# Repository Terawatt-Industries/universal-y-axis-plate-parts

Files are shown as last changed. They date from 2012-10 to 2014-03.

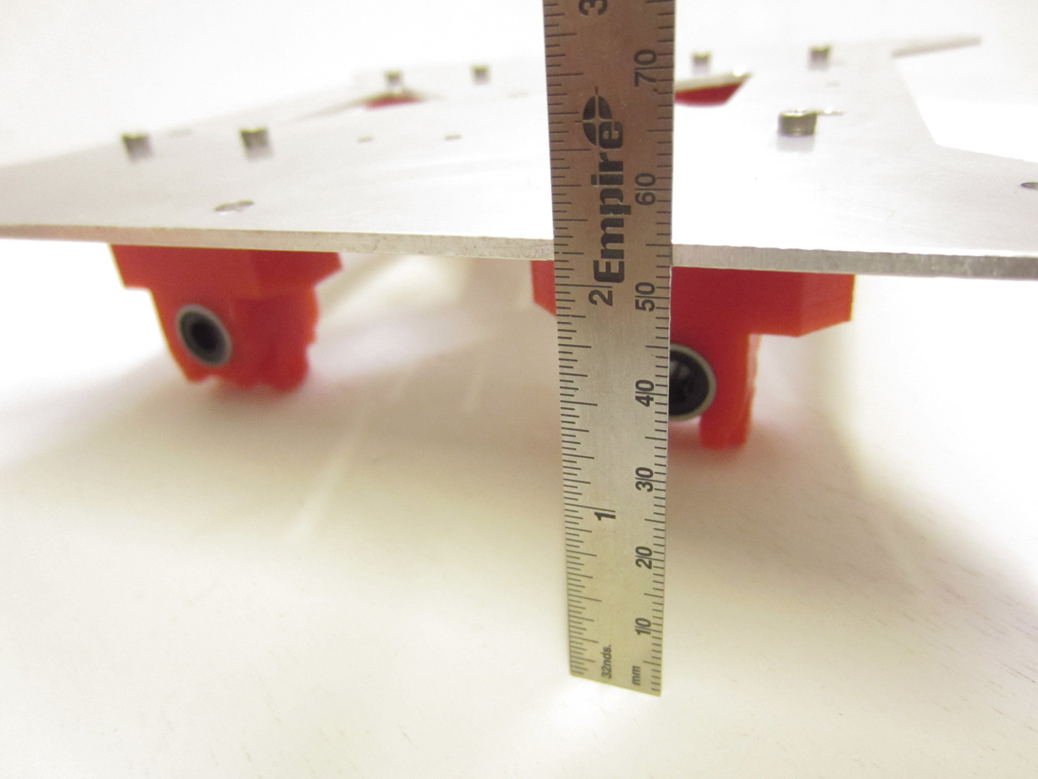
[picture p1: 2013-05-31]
img/plate_with_mounts.JPG

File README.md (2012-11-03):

##Universal Y-Axis Plate
The Universal Y-Axis Plate is an aluminum y-axis plate for RepRap printers, with matching open-source 3D-printed parts to mount it.

The universal plate is designed to eliminate the y-axis plate, and combines both y-axis and heatbed plate holes in one design.  The plate is designed and fulfilled by Terawatt Industries.

This repository contains the matching printed (plastic) parts for the universal plate.  All design files are SCAD with some basic paramterization for height.  There are mounts for LM8UU bearings and tensioners with extra height to keep the belt aligned.

##Bill of Materials
Terawatt fulfills this BOM with 18-8 stainless hardware, but any steel alloy is OK.

1. 1x Universal Y-Axis Plate
2. 8x M3 x 40-45mm socket cap screws
3. 4x M3 x 20-25mm socket cap screws
4. 12x M3 nuts
5. 8x M3 Fender Washer
6. 4x printed LM8UU mount spacers (PLA recommended w/high infill ratio)
7. 4x printed LM8UU mounts (PLA recommended w/high infill ratio)
8. 4x LM8UU bearings

##Assembly Instructions
1. Print up the parts required in PLA, or obtain them.
2. Attach a spacer to the plate with 2x M3x45mm screws.  It may be a tight fit that requires a hex wrench to thread completely.  Then attach the LM8UU mounts on top.
3. Place nuts in the traps and tighten each screw evenly.
4. Repeat steps 2-3 for the other 3 mounts.
5. Push LM8UU bearings into the mounts from the sides.  A bearing press makes the job easier.
6. Place an M3x20mm screw in the mount and a nut in the opposite trap.
7. Tighten the screw.  Be careful not to overtension!  The mount will break if overtensioned - when you hear the plastic stress it's time to stop!
8. Repeat steps 6-7 for each mount.

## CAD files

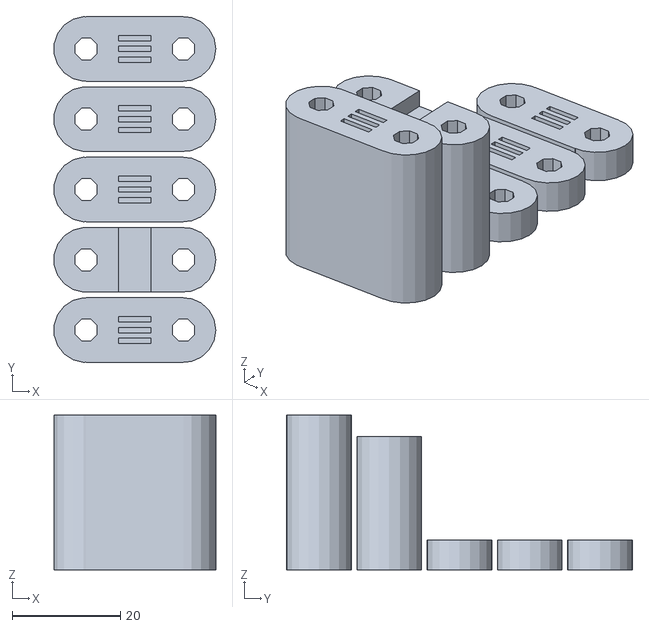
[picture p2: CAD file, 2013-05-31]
dist/belt_tensioner.stl
29.9 x 64.0 x 28.6

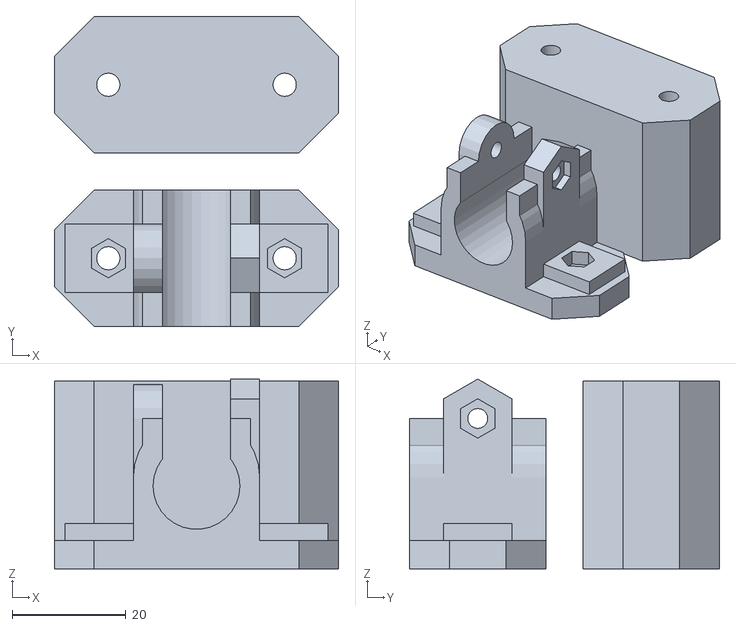
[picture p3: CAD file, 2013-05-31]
dist/lm8uu_with_spacer.stl
50.0 x 54.5 x 33.4

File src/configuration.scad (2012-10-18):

// PRUSA Mendel  
// Configuration file
// GNU GPL v2
// Josef Průša
// josefprusa@me.com
// prusadjs.cz
// http://www.reprap.org/wiki/Prusa_Mendel
// http://github.com/prusajr/PrusaMendel

// PLEASE SELECT ONE OF THE CONFIGURATIONS BELOW
// BY UN-COMMENTING IT

variant=0; //0 for metric
//variant=1; //1 for SAE
if(variant==0){
echo("variant: metric");
}else if(variant==1){
echo("variant: sae");
} else{
echo("WARNING: INVALID CONFIGURATION");
}


vars=[
//[m8_dia, m8_nut, m4_dia, m4_nut, m3_dia, m3_nut, bush_dia, mot_shaft, bush_rod, bush_outerdia, bush_length]
[9,16.4,5,9,4.4,7,11,5.3,8,16,11],//metric
[9,15.7,5.5,10.6,5.5,10.6,11.5,5.3,7.9375,16,11]//SAE
];

//BUSHING TYPE Can generate three versions
// 1 - regular old ones
// 2 - helical ones
// 3 - holders for brass or any other bought bushings
bushing_type = 2;

//Round corner diameter
round_corner_diameter = 8;

//Thin wall size
layer_height = 0.3;
perimeter_width_over_thicknes = 1.6;
infill_widht_over_thickness = 1.55;
thin_wall = 2*(perimeter_width_over_thicknes*layer_height+infill_widht_over_thickness*layer_height);
if(thin_wall<2){
	echo("Check thin wall size, its below 2mm!");
}
echo(thin_wall);

//DO NOT TOUCH THIS SECTION!
m8_diameter = vars[variant][0];
m8_nut_diameter = vars[variant][1];
m4_diameter = vars[variant][2];
m4_nut_diameter = vars[variant][3];
m3_diameter = vars[variant][4];
m3_nut_diameter = vars[variant][5];
bushing_diameter = vars[variant][6];
motor_shaft=vars[variant][7];
bushing_rodsize = vars[variant][8];
bushing_outerDiameter = vars[variant][9];
bushing_lenght = vars[variant][10];


// MINI-HUXLEY VERSION (TODO, just place holder)
// include <configuration-huxley.scad>

// MEGA VERSION (TODO, just place holder)
// include <configuration-mega.scad>


// Some basic functions, probably should be somewhere else
module roundcorner(diameter){
	difference(){
		cube(size = [diameter,diameter,99], center = false);
		translate(v = [diameter, diameter, 0]) cylinder(h = 100, r=diameter, center=true);
	}
}

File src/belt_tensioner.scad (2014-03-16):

// Gregs configuration file
include <configuration.scad>

$fn = 20;

belt_width=6;
belt_thickness=1.5; 
tooth_height=1.5;
tooth_spacing=2;

belt_clamp_thickness=15.5; 
//belt_clamp_width=m3_diameter+3*belt_clamp_thickness+2;
belt_clamp_width = 12;

belt_clamp_hole_separation=18;

belt_clamp_height=m3_diameter+2*belt_clamp_thickness;
belt_clamp_length=belt_clamp_hole_separation+m3_diameter+2*belt_clamp_thickness;

belt_clamp_channel_height=belt_thickness+tooth_height+belt_clamp_thickness*1.4;
belt_clamp_clamp_height=tooth_height+belt_clamp_thickness*1.75;

for (i=[-1])
translate([0,i*(belt_clamp_width+1),0])
belt_clamp(belt_clamp_clamp_height);

belt_clamp_channel(belt_clamp_channel_height);

for (i=[1,2,3])
translate([0,i*(belt_clamp_width+1),0])
belt_clamp(5.5);

module belt_clamp_socket(bch)
{
	difference()
	{
		translate([0,0,bch/2])
		union()
		{
			cube([belt_clamp_hole_separation,belt_clamp_width,bch],center=true);
			for(i=[-1,1])
			translate([i*belt_clamp_hole_separation/2,0,0])
			cylinder(r=belt_clamp_width/2,h=bch,center=true);
		}
		belt_clamp_holes(bch + 2);
	}
}

module belt_clamp_channel(bcchh = belt_clamp_channel_height)
{
	difference()
	{
		translate([0,0,bcchh/2])
		union()
		{
			cube([belt_clamp_hole_separation,belt_clamp_width,bcchh],center=true);
			for(i=[-1,1])
			translate([i*belt_clamp_hole_separation/2,0,0])
			cylinder(r=belt_clamp_width/2,h=bcchh,center=true);
		}

		belt_clamp_holes(belt_clamp_height + 2);

		translate([-belt_width/2,-belt_clamp_width/2-1,bcchh - belt_thickness-tooth_height])
		cube([belt_width,belt_clamp_width+2,belt_thickness+tooth_height+1]);
	}
}

module belt_clamp_holes(height = belt_clamp_height)
{
	translate([0,0,belt_clamp_height/2])
	{
		for(i=[-1,1])
		translate([i*belt_clamp_hole_separation/2,0,0])
		cylinder(r=m3_diameter/2,h=height,center=true);	
	}
}

module belt_clamp(bcch = belt_clamp_clamp_height)
{
	difference()
	{
		translate([0,0,bcch/2])
		union()
		{
			cube([belt_clamp_hole_separation,belt_clamp_width,bcch],center=true);
			for(i=[-1,1])
			translate([i*belt_clamp_hole_separation/2,0,0])
			cylinder(r=belt_clamp_width/2,h=bcch,center=true);
		}
		belt_clamp_holes();
		for(i=[-1:1])
		translate([-belt_width/2,-tooth_spacing/4+i*tooth_spacing,bcch - tooth_height])
		cube([belt_width,tooth_spacing/2,tooth_height+1]);
	}
}

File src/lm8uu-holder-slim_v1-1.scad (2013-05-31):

// LM8UU holder slim v1.1
// *********************************************
// Jonas Kühling
// http://www.jonaskuehling.de
// http://www.thingiverse.com/jonaskuehling
// *********************************************
// derived from:
// http://www.thingiverse.com/thing:14942

// LM8UU/rod dimensions
LM8UU_dia = 15.2;
LM8UU_length = 24;
rod_dia = 8;

//screw/nut dimensions (M3) - hexagon socket head cap screw ISO 4762, hexagon nut ISO 4032
screw_thread_dia_iso = 3;
screw_head_dia_iso = 5.5;
nut_wrench_size_iso = 5.5;


// screw/nut dimensions for use (plus clearance for fitting purpose)
clearance_dia = 0.5;
screw_thread_dia = screw_thread_dia_iso + clearance_dia;
screw_head_dia = screw_head_dia_iso + clearance_dia;
nut_wrench_size = nut_wrench_size_iso + clearance_dia;
nut_dia_perimeter = (nut_wrench_size/cos(30));
nut_dia = nut_dia_perimeter;
nut_surround_thickness = 3;

// main body dimensions
body_wall_thickness = 3.5;
body_width = LM8UU_dia + (2*body_wall_thickness);
body_height = body_width;
body_length = LM8UU_length;
gap_width = rod_dia + 4;
screw_bushing_space = 1;
screw_elevation = LM8UU_dia + body_wall_thickness + (screw_thread_dia/2) +screw_bushing_space;

// TEST - uncomment to render in openscad:
lm8uu_holder(1);		// WITH mountplate
// lm8uu_holder();		// WITHOUT mountplate


// nophead's polyhole module for better lm8uu-fit
module polyhole(d,h) {
    n = max(round(2 * d),3);
    rotate([0,0,180])
        cylinder(h = h, r = (d / 2) / cos (180 / n), $fn = n);
}


module mount_plate()
{
	difference()
	{
		translate([0,0,1.5])
		cube([body_width+2*screw_head_dia+4*nut_surround_thickness,screw_head_dia+2*nut_surround_thickness,3], center=true);

		for(i=[-1,1])
			translate([i*(body_width/2+nut_surround_thickness+screw_head_dia/2),0,-0.5])
				cylinder(r=screw_thread_dia/2, h=4, $fn=20);
	}
}

// main body
module lm8uu_holder(with_mountplate=false)
{
	difference()
	{
		union()
		{
			if (with_mountplate) 
			mount_plate();
	
			// body
			translate([0,0,body_height/4])
				cube([body_width,body_length,body_height/2], center=true);
			translate([0,0,(LM8UU_dia/2)+body_wall_thickness])		
				rotate([90,0,0])
					cylinder(r=(LM8UU_dia/2)+body_wall_thickness, h=LM8UU_length, center=true);
	
			// gap support
			translate([-(gap_width/2)-body_wall_thickness,-(body_length/2),body_height/2])
				cube([body_wall_thickness,LM8UU_length,(LM8UU_dia/2)+screw_bushing_space+(screw_thread_dia/2)]);
			translate([gap_width/2,-(body_length/2),body_height/2])
				cube([body_wall_thickness,LM8UU_length,(LM8UU_dia/2)+screw_bushing_space+(screw_thread_dia/2)]);
	
	
			// nut trap surround
			translate([gap_width/2,0,screw_elevation])
				rotate([0,90,0])
					cylinder(r=(((nut_wrench_size+nut_surround_thickness*2)/cos(30))/2), h=(body_width-gap_width)/2, $fn=6);
			translate([gap_width/2+(body_width-gap_width)/4,0,screw_elevation/2])
				cube([(body_width-gap_width)/2,nut_wrench_size+(nut_surround_thickness*2),screw_elevation],center=true);

			// Screw hole surround
			translate([-gap_width/2,0,screw_elevation])
				rotate([0,-90,0])
					cylinder(r=(screw_head_dia/2)+nut_surround_thickness, h=(body_width-gap_width)/2, $fn=20);
			translate([-(gap_width/2+(body_width-gap_width)/4),0,screw_elevation/2])
				cube([(body_width-gap_width)/2,screw_head_dia+(nut_surround_thickness*2),screw_elevation],center=true);
		}
	
		// bushing hole
		translate([0,0,LM8UU_dia/2+2])
			rotate([90,0,0])
//				cylinder(r=LM8UU_dia/2, h=LM8UU_length+1, center=true);
				translate([0,0,-(LM8UU_length+1)/2]) polyhole(LM8UU_dia,LM8UU_length+1);	// TESTING POLYHOLE MODULE FOR BETTER LM8UU FIT
	
		// top gap
		translate([-(gap_width/2),-(body_length/2)-1,body_height/2])
			cube([gap_width,LM8UU_length+2,(LM8UU_dia/2)+screw_bushing_space+(screw_thread_dia/2)+(nut_dia/2)+nut_surround_thickness+1]);
	
		// screw hole (one all the way through)
		translate([0,0,screw_elevation])
			rotate([0,90,0])
				cylinder(r=screw_thread_dia/2, h=body_width+3, center=true, $fn=20);
	
		// nut trap
		translate([gap_width/2+body_wall_thickness,0,screw_elevation])
			rotate([0,90,0])
				cylinder(r=nut_dia/2, h=body_width/2-gap_width/2-body_wall_thickness+1,$fn=6);
	
		// screw head hole
		translate([-(gap_width)/2-body_wall_thickness,0,screw_elevation])
			rotate([0,-90,0])
				cylinder(r=screw_head_dia/2, h=body_width/2-gap_width/2-body_wall_thickness+1,$fn=20);
	
	}
}

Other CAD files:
src/lm8uu_with_spacer.scad

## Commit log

2012-10-11 first commit; added printed LM8UU mounts as pictured - M3 holes are spaced within 0.5mm but nuttrap dimension isn't right; still deciding license for SVG source;
    [lm8uu-holder-slim_v1-1.scad, lm8uu_with_spacer.scad, lm8uu_with_spacer.stl]
2012-10-12 fixed M3 nut traps and tightened spacing between M3 screws 0.125mm from in-the-field;
    [lm8uu_with_spacer.scad, lm8uu_with_spacer.stl]
2012-10-18 added y-plate belt tensioner for GT2 2mm pitch default; M3 screw holes in spacer were too tight - captive nut holes way too tight -- added more space but still might be tiny-off;
    [belt_tensioner.scad, configuration.scad, lm8uu_with_spacer.scad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]
2012-11-03 added ~8mm height to 2x tensioner and 4x mount spacers;
    [belt_tensioner.scad, belt_tensioner.stl, lm8uu_with_spacer.scad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]
2012-11-03 got rid of extraneous matching_parts parent;
    [belt_tensioner.scad, belt_tensioner.stl, configuration.scad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]
2012-11-03 fs cleanup for gh-pages pub;
    [belt_tensioner.scad, belt_tensioner.stl, configuration.scad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]
2012-11-03 more fs cleanup for gh-pages;
    [belt_tensioner.scad, belt_tensioner.stl, configuration.scad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]
2013-05-31 added extra clearance - you may want to reduce depending on printer calibration;
    [belt_tensioner.scad, belt_tensioner.stl, lm8uu-holder-slim_v1-1.scad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]
2013-05-31 added LICENSE header;
    [lm8uu_with_spacer.scad]
2014-03-16 added module param defaults;
    [belt_tensioner.scad, lm8uu_with_spacer.scad]
